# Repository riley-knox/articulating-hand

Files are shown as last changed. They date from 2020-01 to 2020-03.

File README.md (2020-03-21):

# articulating-hand

Hand Complete

### Table of Contents

1. Package Contents
2. Necessary Components
3. Assembly
4. ROS Structure
5. Operation
6. Troubleshooting

### Package Contents

- Bill of materials
- CAD files
- Laser cutter profiles
- Arduino sketches
- ROS directories and files
    - /config
        - RViz configuration file
    - /launch
        - Program launch file
    - /model
        - **.yaml** files holding geometric parameters
        - **.xacro** files to build robot model
    - /msg
        - Custom message files for servo-driving communication
    - /nodes
        - **slider_gui**: GUI initialization script
        - **update_joints**: servo position -> joint angle conversion algorithm
    - CMakeLists.txt
    - package.xml

### Necessary Components

See Bill of Materials for specific part designations.

- Arduino Uno (1)
- USB cable Type A/B (1)
- Servo driver board (1)
- 3/32" acrylic sheet (1)
- Servo motors (11)
- Screws (don't know exact sizes/numbers right now [3/20/20] because I can't go into the lab to count due to COVID-19 but will update)

### Assembly
#### Printed Parts

Component files provided in .stl form for easy 3D printing. If multiple files exist for the same part, use the file with the highest version number.

Print parts with 0.1mm layer height for best results. Print all pieces with largest flat side touching print bed (see below). Use 25% infill with an appropriate pattern to prevent flat surfaces from sagging. Use supports.

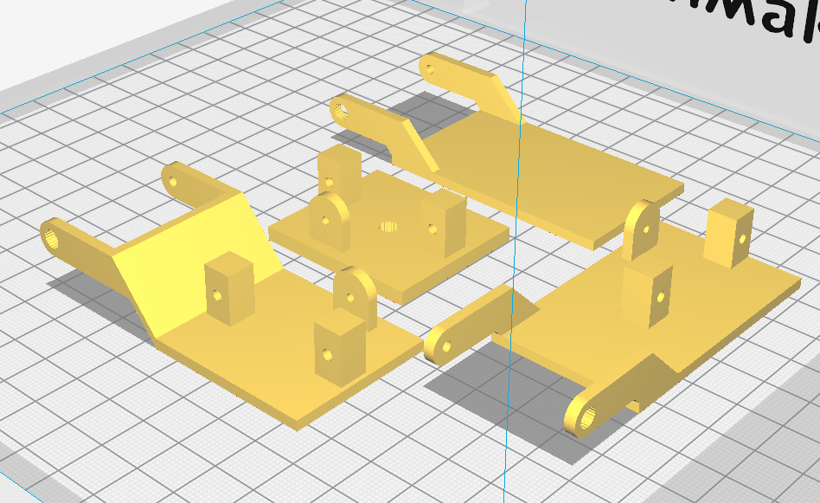
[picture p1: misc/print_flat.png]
Print Bed


**Number of Pieces to Print:**
- Distal finger: 5
- Proximal finger: 4
- CMC joint small: 1
- CMC joint big: 1

#### Laser-Cut Parts

Cut both profiles in /Laser_Cut out of 3/32" acrylic.

**Number of Pieces Produced:**
- Angled mounting tab: 8
- Square stabilizing tab: 4
- Palm: 1

#### Construction

Note: tap all holes before inserting screws!

Assemble fingers left to right (pinky finger -> index finger direction) for ease of assembly.

Mount servo motors to proximal finger pieces using screws. Attach distal finger pieces to servo knobs via press-fit. Connect distal finger piece to proximal finger piece using screw through stabilizing tab.

Insert two angled mounting tabs through paired slots in palm. Attach servo to tabs using screws. Servo will have some up-and-down "wiggle room" but should not pull away from palm. Attach square stabilizing tab to proximal finger tab using screw. Insert stabilizing tab into single slot in palm and slide forward so slot engages with palm. Attach proximal finger piece to servo by press-fitting tab onto servo knob. Repeat process for all four fingers.

Insert servo into thumb slot and drill mounting holes. Attach to palm using screws. Mount servo to small CMC joint piece using screws. Mount servo to big CMC joint piece using screws. Attach distal finger piece to big CMC joint piece via press-fit and screw in stabilizing tab. Attach big CMC joint piece to small CMC joint piece via press-fit and screw in stabilizing tab.Connect small CMC joint piece to palm by press-fitting onto mounted servo knob.

#### Electrical Connections

Connect Arduino to your computer using USB cable.

Connect servo plugs to driver board per joint numbering convention shown below.

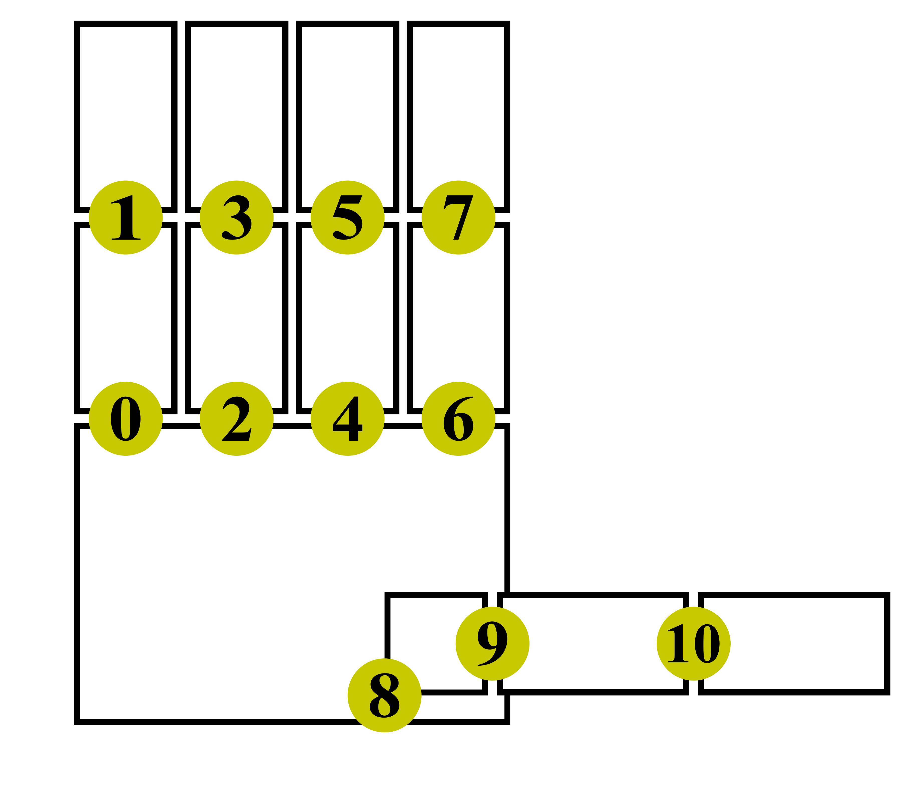
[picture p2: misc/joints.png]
Joint #s


Connect servo driver board to Arduino:

| Arduino pin | Driver board pin |
|:---:|:---:|
| 5V | VCC |
| GND | GND |
| A4 (SDA) | SCL |
| A5 (SCL) | SDA |

Connect driver board to wall power using the plug.

### ROS Structure
#### Nodes
- /converter
    - Creates ROS JointState messages from servo position commands
    - Publishers: `joint_states`
    - Subscribers: `servo_cmd`
- /slider_bar_gui
    - Creates and updates the control GUI window
    - Generates commands to drive servos
    - Publishers: `servo_cmd`
    - Subscribers: None
- /arduino
    - Creates joint motion via PWM signals in response to command
    - Publishers: None
    - Subscribers: `servo_cmd`
- /robot_state_publisher
    - Makes the robot state (ex: position and velocity) available for motion planning, visualization, and simulation
- /rviz
    - Provides visualization for robot positioning

#### Topics/Types
Note: only custom types written for this package are included here.

- `servo_cmd`: custom message type `ServoArray`, array of 2-vectors each holding a servo number and position; allows for compact communication by holding all servo position commands in one message

### Operation
#### Launching/Exiting Program:
1. Navigate to workspace root directory
2. `catkin_make`
3. `source devel/setup.bash`
4. `roslaunch articulating_hand hand_bot.launch` (can be done from any directory location in same terminal window)
5. `Ctrl+C` in same terminal window to exit

#### Joint Control
*Using GUI (recommended):* <br>
&nbsp;&nbsp;&nbsp;&nbsp;Click and drag slider bars in GUI window to move joints.

*Publishing message from command line:* <br>
&nbsp;&nbsp;&nbsp;&nbsp;In a new terminal window, `rostopic pub /servo_cmd articulating_hand/ServoDrive <servo_number> <servo_position> --once`. <br>
&nbsp;&nbsp;&nbsp;&nbsp;This method is not recommended, as it cannot detect whether you are attempting to (a) drive a servo that does not exist, or (b) drive a servo beyond its physical operating limits.

### Troubleshooting

When uploading sketch to Arduino:
- *ioctl("TIOCMSET"): Protocol error*<br>
    &nbsp;&nbsp;&nbsp;&nbsp;Unplug USB cable and plug back in

Common ROS Error:
- *Unable to sync with device; possible link problem...*<br>
    &nbsp;&nbsp;&nbsp;&nbsp;Usually caused by baud rate mismatch between Arduino and ROS. Outbound baud rate is set in **hand_bot.launch** under <node name="arduino"...>; inbound baud rate is set in **servo_controller.ino** by command `nh.getHardware()->setBaud(BAUD)`. Make sure these match.

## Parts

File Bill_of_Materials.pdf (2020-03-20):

Articulating Robot Hand Bill of Recommended Materials

Part Name | Number | Vendor
Arduino Uno | 1 | Arduino
USB 2.0 Cable Type A/B | 1 | Arduino
16-Channel 12-bit PWM/Servo Driver | 1 | Adafruit
Analog Feedback Micro Servo | 11 | Adafruit
Acrylic Sheet, 3/32” Thickness | 1 | McMaster-Carr
PLA 3D Printing Filament Spool | 1 | Ultimaker

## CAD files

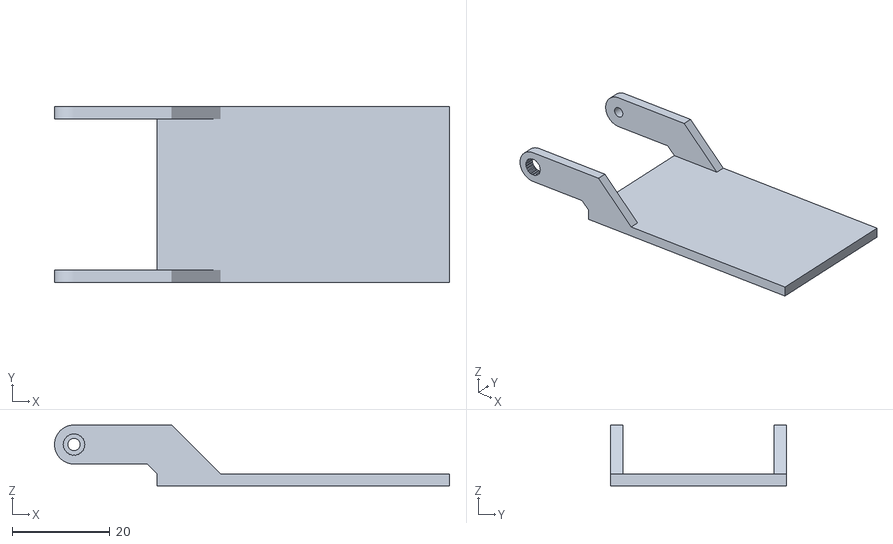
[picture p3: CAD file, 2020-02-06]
CAD/fing_dist_v6.stl
81.0 x 36.0 x 12.5

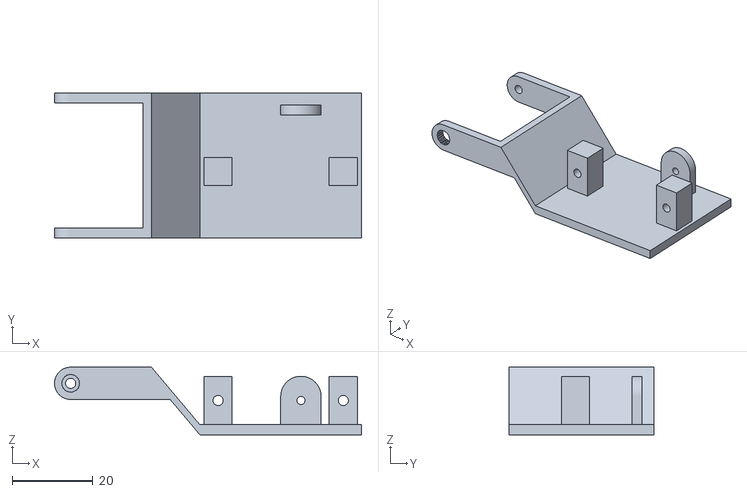
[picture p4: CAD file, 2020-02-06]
CAD/CMC_big_v1.stl
76.0 x 36.0 x 16.8

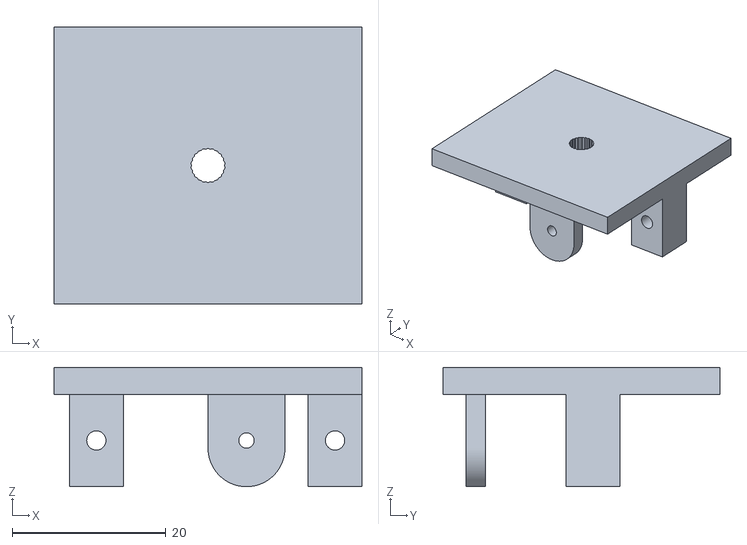
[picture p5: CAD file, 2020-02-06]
CAD/CMC_small_v1.stl
40.0 x 36.0 x 15.5

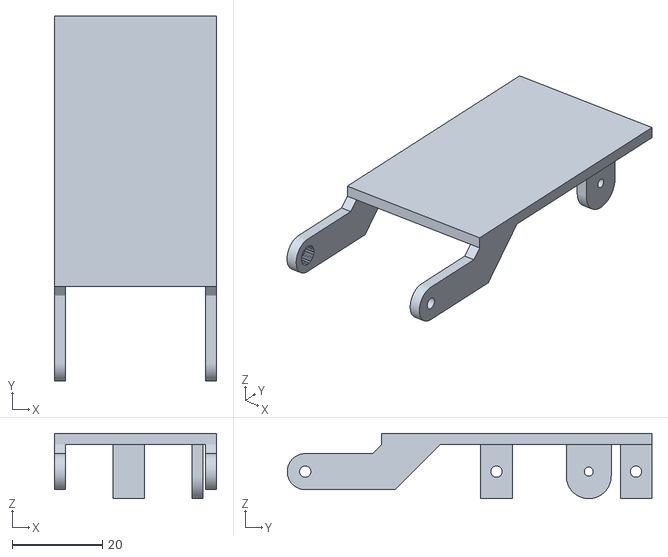
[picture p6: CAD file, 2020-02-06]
CAD/fing_prox_v6.stl
36.0 x 81.0 x 14.5

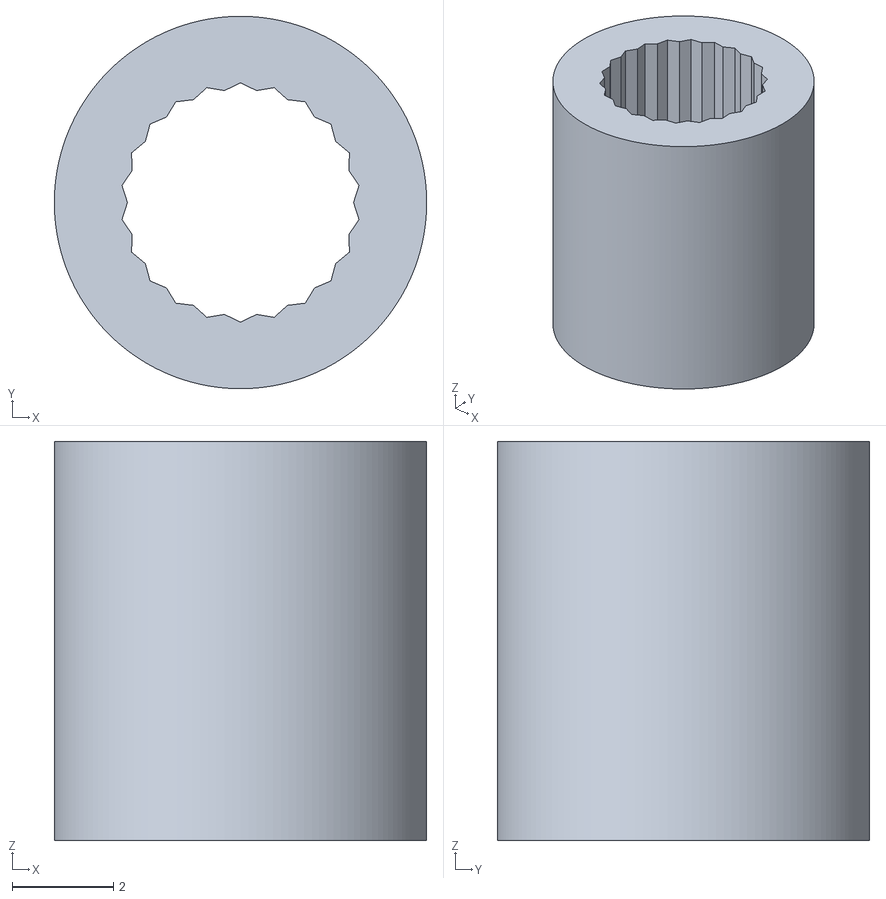
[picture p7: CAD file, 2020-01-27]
CAD/servo_knob_pressfit_v2.stl
7.35 x 7.35 x 7.88

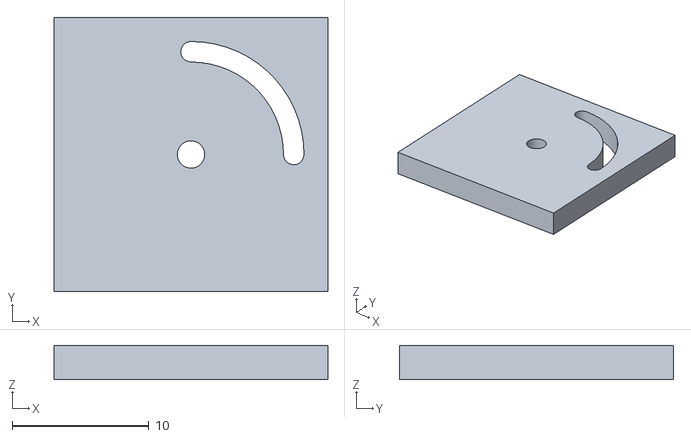
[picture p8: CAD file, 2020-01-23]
CAD/disk_attachment_test_piece.stl
20.0 x 20.0 x 2.50

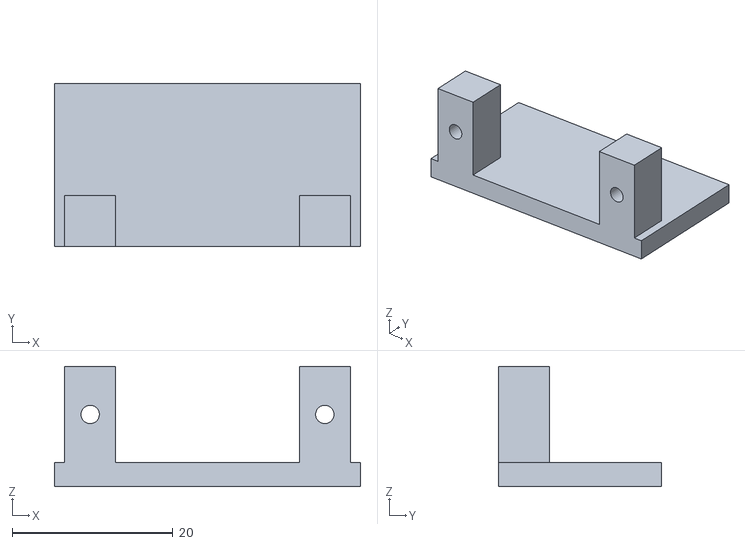
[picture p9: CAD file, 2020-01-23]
CAD/servo_mounting_bracket_v1.stl
38.1 x 20.3 x 15.0

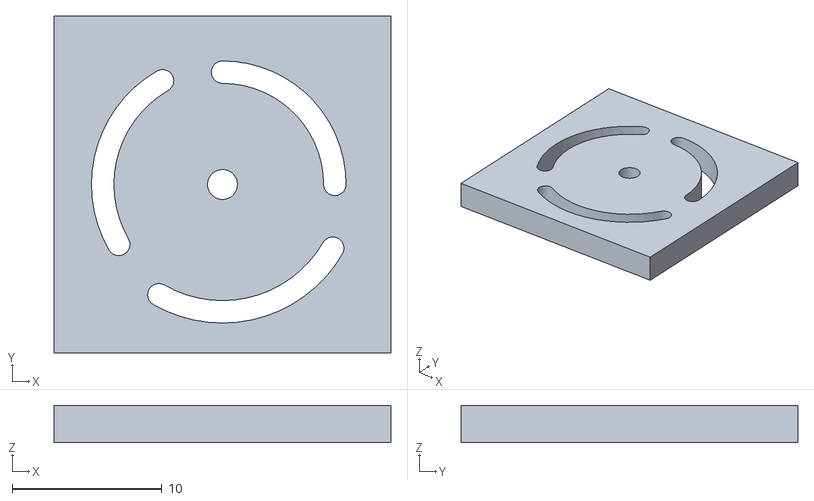
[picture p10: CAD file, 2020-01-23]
CAD/disk_attachment_test_piece_v2.stl
22.5 x 22.5 x 2.50

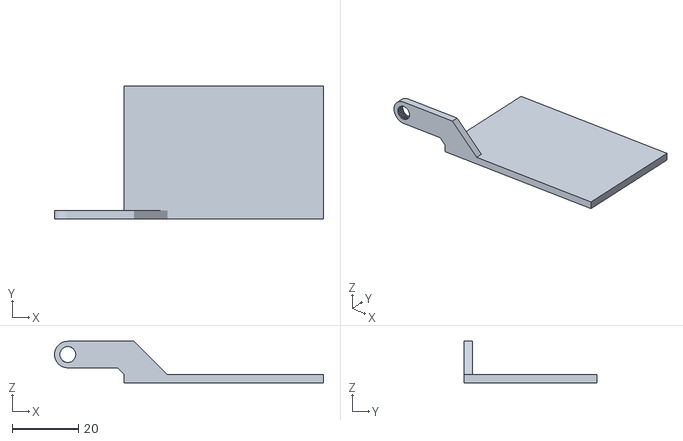
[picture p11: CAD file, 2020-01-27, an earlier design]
CAD/fing_dist_v4.stl
81.0 x 40.0 x 12.5

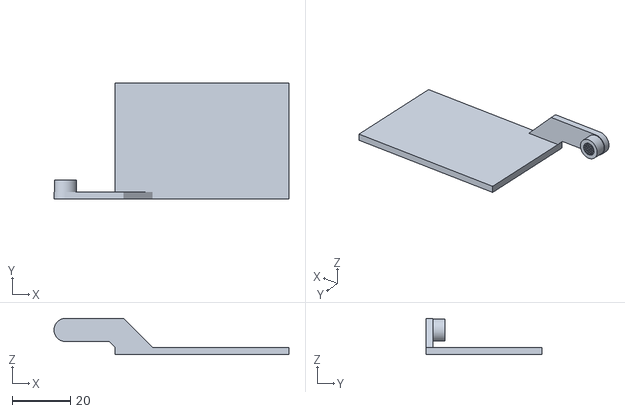
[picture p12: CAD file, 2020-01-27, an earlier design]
CAD/fing_dist_v3.stl
81.0 x 40.0 x 12.5

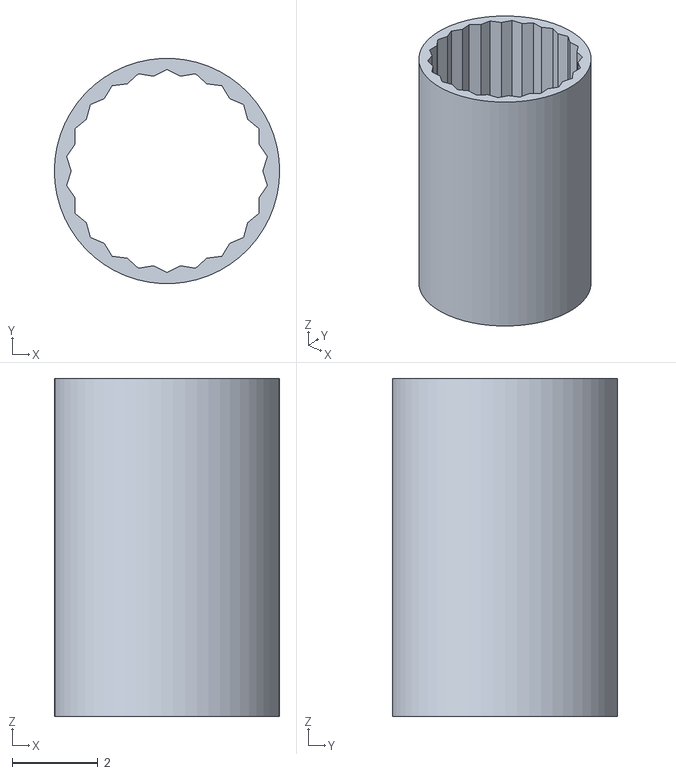
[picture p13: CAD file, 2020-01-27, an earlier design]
CAD/servo_knob_pressfit_v1.stl
5.25 x 5.24 x 7.88

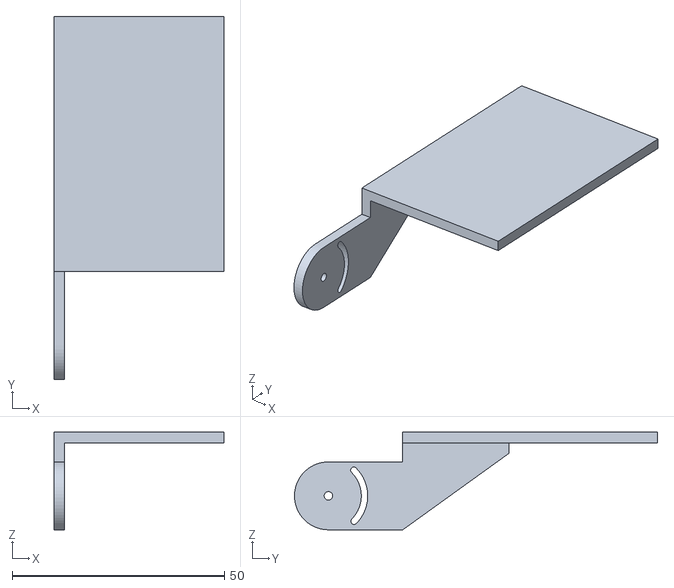
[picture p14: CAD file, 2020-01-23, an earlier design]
CAD/fing_prox_v3.stl
40.0 x 85.5 x 23.0

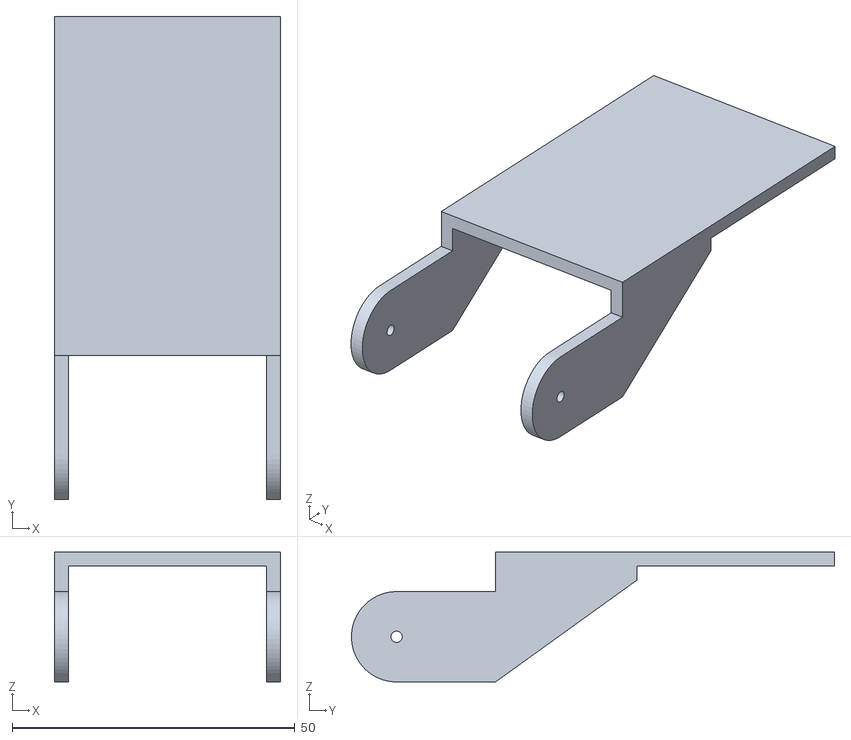
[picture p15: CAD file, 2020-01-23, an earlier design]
CAD/fing_prox_v2.stl
40.0 x 85.5 x 23.0

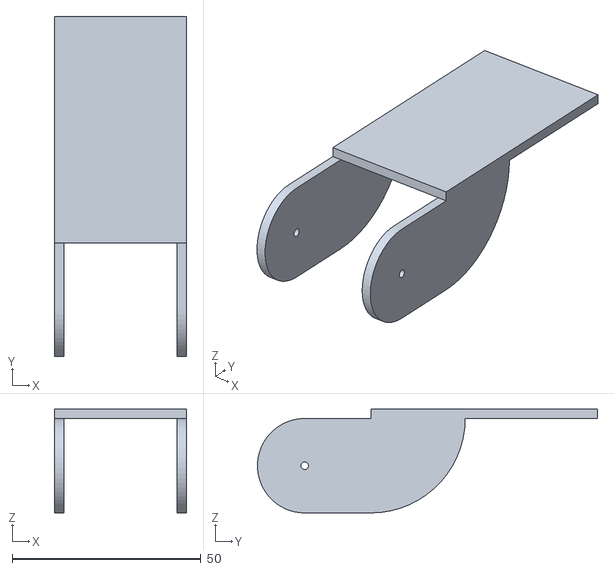
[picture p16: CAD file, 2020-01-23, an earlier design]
CAD/fing_prox_v1.stl
35.0 x 90.0 x 27.5

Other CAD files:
CAD/fing_prox_v5.stl
CAD/fing_dist_v5.stl
CAD/fing_dist_v2.stl
CAD/fing_dist_v1.stl
CAD/fing_prox_v4.stl

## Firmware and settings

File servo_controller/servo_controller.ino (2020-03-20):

#include <ros.h>
#include <Servo.h>            // PROBABLY DON'T NEED, MAYBE DELETE WHEN CLEANING UP ROS NODE
#include <Adafruit_PWMServoDriver.h>
#include <articulating_hand/ServoArray.h>

#define SERVO_FREQ 50
#define SERVO_MIN 10
#define SERVO_MAX 5000
#define NUM_SERVOS 11
#define BAUD 115200

// instantiate node handle; allows publisher/subscriber creation and handles serial communication
ros::NodeHandle nh;

// instantiate servo driver board interfacing
Adafruit_PWMServoDriver srvDrvr = Adafruit_PWMServoDriver();

// actuation callback function
void servo_callback(const articulating_hand::ServoArray& cmd){
  for (int i = 0; i < NUM_SERVOS; i++){
    uint8_t servoNum = cmd.srv_comms[i].servo_num;           // servo number
    uint16_t servoPos = cmd.srv_comms[i].servo_pos;          // servo position

    srvDrvr.setPWM(servoNum, 0, servoPos);
  }
}

// initialize subscriber
ros::Subscriber<articulating_hand::ServoArray> servo_sub("servo_cmd", &servo_callback);

void setup() {
  nh.getHardware()->setBaud(BAUD);      // initialize serial communication; baud = 115200

  nh.initNode();            // initialize node

  nh.subscribe(servo_sub);  // initialize subscriber

  srvDrvr.begin();
  srvDrvr.setOscillatorFrequency(27000000);
  srvDrvr.setPWMFreq(SERVO_FREQ);
}

void loop() {
  nh.spinOnce();
  delay(1);
}

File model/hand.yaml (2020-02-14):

# geometric parameters for the articulating hand robot

palm_width: 0.160
palm_height: 0.125

finger_segment_length: 0.06
finger_segment_width: 0.036

cmc_length: 0.036
cmc_width: 0.04

thumb_prox_length: 0.04

thickness: 0.0025
cmc_thickness: 0.0035

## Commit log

2020-01-23 Adding CAD files
    - CAD/
    Folder to hold CAD design files
    - .gitignore
    Ignoring .pdf and .odt files
    [disk_attachment_test_piece.stl, disk_attachment_test_piece_v2.stl, fing_dist_v1.stl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]
2020-01-27 More CAD files
    - Versions of distal finger, proximal finger, and servo knob press-fit tester pieces
    [fing_dist_v2.stl, fing_dist_v3.stl, fing_dist_v4.stl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]
2020-02-06 CAD Upload #3
    New versions of proximal & distal finger segments
    Adding big & small CMC joint pieces
    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
    [CMC_big_v1.stl, CMC_small_v1.stl, fing_dist_v6.stl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]
2020-02-11 Adding laser cut profiles
    [lasercut_tabs.dxf, palm.dxf, servo_tab.dxf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]
2020-02-14 Starting ROS Integration
    - RViz build complete but may need to tweak later
    - Created CMakeLists.txt and package.xml
    - config/hand_bot.rviz
    RViz configuration file
    - launch/hand_bot.launch
    Opens robot_state_publisher
    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
    [hand.xacro, links_and_joints.xacro]
2020-02-17 Custom ServoDrive message
    - Fixed CMakeLists.txt to allow custom message generation
    - Created ServoDrive custom message
    Two fields: servo # and angle to set
    - Integrated custom message with servo_controller.ino
    [servo_controller.ino]
2020-02-18 Servo control via publisher
    Launches Arduino as node with correct port & baud rate
    - servo_controller.ino
    Initializes servo driver board criteria
    Subscriber callback:
    Pulls message inputs and checks for validity
    Lights appropriate LED (onboard/external)
    Sets servo position
    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
    [servo_controller.ino]
2020-02-21 Updating README
    - Updated README.md with operation and debugging info
    Comments and stuff
    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
2020-02-26 Model updates in RViz
    - CMakeLists.txt
    Added update_joints node to install() section
    - get_positions.ino
    Created script to get feedback from servos on Arduino
    Added comments saying to delete stuff
    Opens 'converter' node
    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
2020-02-26 Sliders GUI built
    Added nodes/slider_gui to install()
    Added slider_bar_gui node
    Added names.yaml to parameter server
    Removed joint_state_publisher nodes
    - model/limits.yaml
    Added placeholder range to broken servo entry (odd numbers)
    - model/names.yaml
    Created file with list holding joint names
    - nodes/slider_gui
    Opens GUI showing slider bars for joint control
    No integration with other nodes yet
    - nodes/update_joints
    Loads list of joint names from parameter server
    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
2020-03-03 Slider bars control RViz
    Changed viewpoint or whatever
    Updated rosparam line to load correct .yaml file (see below) upon launch
    - model/joint_state_init.yaml
    Renamed from model/names.yaml
    Created element defining initial joint/servo positions
    Loads initial servo positions
    Places slider bar objects in list to allow access to joint positions
    Initializes publisher on topic /servo_cmd
    Sets initial positions of slider bars
    Created servo_move function to drive servo motion from slider bar control
    Replaced root.mainloop() with root.upd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
2020-03-03 Comments in joint_state_init.yaml
    - Added comments indicating what each line in the joint_inits parameter represents
2020-03-03 Real-time joint updates in RViz
    Added function docstrings
    Replaced timing variables with 1/100 second rospy.sleep() command
    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
2020-03-04 Real-time control working!
    Added ServoArray.msg to add_message_files()
    Launch Arduino node with baud=115200
    - msg/ServoArray.msg
    Created message type to hold all servo commands simultaneously
    Publish on topic /servo_cmd with type ServoArray
    Adapted servo_move() function to deal with ServoArray message type
    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
2020-03-16 Removing unnecessary Arduino files
2020-03-19 Building out README
    - Laser_Cut/all_tabs.svg
    Updated to include fourth stabilizing tab
2020-03-19 Trying to remove stuff
    [lasercut_tabs.dxf]
2020-03-19 Removing more stuff
    [palm.dxf, servo_tab.dxf, stabilizer.dxf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]
2020-03-20 Final commit hopefully
    - Finished README.md
    - Cleaned up node files
    Removed excess comments, etc
    Added .svg files
    - Added joint numbering image to /misc
    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
2020-03-20 Uploaded BOM
